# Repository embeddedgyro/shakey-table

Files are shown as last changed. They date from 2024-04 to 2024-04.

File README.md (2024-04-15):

# Introduction
Welcome to the shakey-table GitHub page, developed by Adam Englebright, Torin Storkey, Gennady Magin, and Jambulingam Kothandapani.

As part of the Real Time Embedded Programming 5 course at the University of Glasgow,
we have been tasked with developing a project that requires real time programming under GNU/Linux on a Raspberry Pi.
The project we have decided on is a self-balancing cup holder, implemented using a reaction wheel.
Essentially, an inverted pendulum. This git repository contains the code required to run this
self-balancing cup holder and instructions on how to build it for both software and hardware.

We used a Pi 5, which introduced some extra challenges as its GPIO differs greatly from
previous versions, meaning that common libraries like `pigpio` would not work.
This project was only tested on a Pi 5 using the latest Raspberry Pi OS
(`uname -a` output: *Linux rpi5-2 6.6.21-v8-16k+ #1 SMP PREEMPT Tue Mar 12 11:01:10 UTC 2024 aarch64 GNU/Linux*).
We cannot guarantee that it will work on other versions of the Pi or on other operating systems
or OS versions.

# Software
## Prerequisites/Dependencies
The following Debian packages (Raspberry Pi OS is built on Debian and has access to Debian packages) are required for this program to build and run on a rpi5:
* `linux-libc-dev`
* `libi2c-dev`
* `make`
* `cmake`
* `g++`

The following packages are recommended:
* `git` for cloning the repository, although you can simply download the code from the GitHub website if you wish.
* `doxygen` for creating nice documentation from the comments in the code.
* `texlive-full` for compiling a PDF document from the LaTeX code created by Doxygen (which also creates a website that you can view in your browser,
so this is not necessary to view the documentation).

These packages can be installed using `sudo apt install <package name>`.

There are also installs required that cannot be found in the standard repos, primarily due to the use of a Pi 5:
* `libgpiod` v2 is required. However, the version on the Debian Bookworm repo as of 2024-03-03 is v1.6.3 (despite the package name being `libgpiod2`).
This must be installed from source. `git clone git://git.kernel.org/pub/scm/libs/libgpiod/libgpiod.git`
([repo link](https://git.kernel.org/pub/scm/libs/libgpiod/libgpiod.git/)) in a suitable place and follow the `README` instructions.
The advised options to pass to the `autogen.sh` script are `--enable-tools=yes` (not *necessary*, but provides useful command line tools)
and `--enable-bindings-cxx` (**necessary**, since this is a C++ program). Note that to build with C++ bindings, the `autoconf-archive` package is required
(this can be easily `apt install`'d from the Debian repos). You may also need to `apt install` the `libtool` package for the build to work.
* As of the latest kernel for the Pi 5 on 2024-04-03 (6.6.21-v8-16k+), this patch is required for PWM to work through the sysfs interface:
[https://github.com/raspberrypi/linux/pull/6026](https://github.com/raspberrypi/linux/pull/6026). Install using `sudo rpi-update pulls/6026`.
See [https://forums.raspberrypi.com/viewtopic.php?t=359251](https://forums.raspberrypi.com/viewtopic.php?t=359251),
particularly the [post by neuralassembly](https://forums.raspberrypi.com/viewtopic.php?p=2202349#p2202349) and onward.

### config.txt
To enable the I2C and PWM hardware on the Raspberry Pi 5, the following lines must be added to your `/boot/firmware/config.txt`:
* `dtparam=i2c_arm=on`
* `dtparam=i2c_vc=on,i2c_vc_baudrate=400000`
* `dtoverlay=pwm-2chan`

Remember to reboot your Pi after entering these lines. The `config.txt` used on our Pi can be found in the root of this repo.

## Building the Software
To build the software, follow these instructions:
* `git clone https://github.com/embeddedgyro/shakey-table.git`
* `cd shakey-table`
* `mkdir build` (It is advisable to create an *out-of-source* build, hence this and the following step.)
* `cd build`
* `cmake ..`
* `make`

After this, an executable program called **ShakeyTable** should exist under the `build/src/` directory.
That is, `build/src/ShakeyTable`. This program can be run by entering either the absolute or relative
path of the executable. For example, `/some/path/from/root/shakey-table/build/src/ShakeyTable`, or
`src/ShakeyTable` if you are still in the `build` directory. If you are in the same directory as the
executable, you can enter `./ShakeyTable` (the leading dot means *this directory*).

In addition to the main **ShakeyTable** executable, there will also be a **ShakeyTable_no_INA**
executable. This runs a version of the main program that doesn't use the INA260 current sensor
for torque control. Instead, it only uses the MPU6050 and a single PID controller for position control.
This program was developed as a backup in case the INA260 could not be configured to
work with the motor driver operating in both directions
([see the wiki](https://github.com/embeddedgyro/shakey-table/wiki/Hardware-Woes#the-ina260-current-sensor)).

There will also be two executables for testing the functionality of the MPU6050 and INA260,
named **mpu_testing** and **ina_testing**, respectively. **mpu_testing** will communicate with
the MPU6050 and continuously write the measured angular position to the screen.
**ina_testing** will do the same with the INA260, continuously writing out the measured
current to the screen. These test programs are useful for confirming that the sensors
have been correctly connected to the Pi and are functioning properly.

## Documentation
Documentation of this project is provided by Doxygen formatted comments in the code.
Doxygen can be used to create a website and PDF document that organise the documentation
in a way that is clear, easy to navigate, and easy to read.

### Master Release Documentation
To see the the documentation for the latest release of shakey table the documentation can be found [here](https://shakeytable.guengineering.co.uk/).

### Self Hosted Website
To create the documentation website for personal forks and development builds, run `make doc` after the `cmake ..` command from the above build instructions.
Running `cmake ..` will create a Doxyfile, and running `make doc` will run Doxygen on this file to generate
the documentation website under the `build/html/` directory.

To view this website, open your browser of choice.
In the URL bar, enter `file:///some/path/from/root/shakey-table/build/html/index.html`. This will open the
main page of the website. From there you can find the rest of the documentation using the navigation
tools at the top of the page.

### PDF Document
After running `make doc`, there will also be a `build/latex/` directory. If you have a TeX distribution
installed, you can `cd` into this directory and enter `make`. This will invoke `pdflatex` to generate
a PDF document called `refman.pdf`, which will contain the Doxygen generated documentation for the project.
View with your PDF reader of choice. Most browsers can also view PDF documents.

# Unit Testing
ShakeyTable on the whole has three modules namely `MPU6050`, `INA260` and `Cytron MD20A` along with PID control functionality. When developing unit testing we intend to validate each module's functionalities by a specific set of test cases and consolidated them into `Online` and `Offline` testing based on its nature of examination. Online unit testing validates  each module's communication status to raspberry pi through i2c bus. Hence to run online testing each module has to be configured into the overall setup and actively involved in communication. On the other hand offline testing intend to validate the static functionalities of the software, examining the expected output against the module's program output. These testing can be validated when the setup is offline to ensure proper functioning of the software.
	
## Building Unit Tests
Follow the software building procedure as mentioned before which includes cloning the repo and building the system through commands `cmake .. make`. This will generate the executable files for each module's unit testing functions. Now type `ctest` in the same directory to view the results of both online and offline testing together. You can also view the results of either one testing through the command `ctest -R online` or `ctest -R offline` which executes only the files associated to those testing. Individual executable files for concern modules can be found in the directory `./test/****/**`. Here `./` indicates that you are required to be currently in `build` directory and `****` indicates the module that you intended to view the executables (eg., mpu6050, ina260) and `**` specifies the specific test file executable.
	eg., `./test/mpu6050/mpu6050_AccelOffset_ut`.

## Unit Testing Output
Each unit test will either pop `Passed` if successfully executed without exception or `Subprocess aborted***Exception:` with the exception scenario encountered if failed.

# Hardware

## Components

This section describes hardware components used in this project, and what is their purpose. Descritions are followed by links to datasheets for those components and information about how they should be wired and positioned on a physical prototype. All supporting reference images for this section can be found in "Hardware Assembly" section of this README.

The following components were used for this project:

* Microcontroller - Raspberry Pi 5. Used for executing the main program and interfacing with sensors and motor driver.

Documentation for it can be found here [https://www.raspberrypi.com/documentation/](https://www.raspberrypi.com/documentation/).

* Current Sensor - INA260. Used for reading current flowing through the motor for PID motor control as current is proportional to the torque generated by the motor. Uses I2C communication protocol for interfacing with Pi.

Datasheet can be found here [https://www.ti.com/lit/ds/symlink/ina260.pdf](https://www.ti.com/lit/ds/symlink/ina260.pdf).

Should be connected in series with the motor. Vin- terminal is connected to the white wire on the motor and Vin+ is connected to the MB terminal of the motor driver. Powered by a 3V3 supply from the Pi. Communicates with the Pi through I2C1 pins (SDA->gpio0, SCL->gpio1) which don't have internal pull-up resistors, but there are pull-up resistors inside the current sensor, so that should not be a problem. The Alert pin is connected to gpio5 on the Pi.

* Gyro-Acelerometer Sensor - MPU6050. Measures the acceleration of the table in a 2D plane and subtracts the centripetal acceleration from it to get the acceleration due to gravity. Measurements are used for PID motor control. Uses I2C communication protocol for interfacing with Pi.

Datasheet can be found here [https://mm.digikey.com/Volume0/opasdata/d220001/medias/docus/2204/SEN0142_Web.pdf](https://mm.digikey.com/Volume0/opasdata/d220001/medias/docus/2204/SEN0142_Web.pdf).

Should be mounted firmly to the surface of the table with connection pins facing the ground. Position reference image can be found in "Hardware Assembly" section of the README. Powered by a 3V3 supply from the Pi. Communicates with the Pi through I2C0 pins (SDA->gpio2, SCL->gpio3) which have internal pull-up resistors. No extra external circuitry is needed. Interrup pin should be connected to gpio4.

* Motor Driver - Cytron MD20A. Regulates voltage supplied to the motor. Controls the direction and speed of motor rotation with PWM.

Datasheet can be found here [https://robu.in/wp-content/uploads/2019/05/MD20A-Datasheet.pdf](https://robu.in/wp-content/uploads/2019/05/MD20A-Datasheet.pdf).

Uses a 12V external DC power supply connected to VA+ and VB- for delivering power to the motor. In this project, an external power generator was used for this purpose. Use thick multicore wires with good isolation for power lines. Controls the motor rotation by receiving a 20kHz PWM signal with a PID-controlled Duty Cycle from gpio18 on the Pi. Direction is controlled by a High-Low output from gpio23 into the DIR pin on the motor driver.

* Motor - 12V DC Motor 12kg-cm 350RPM w/Encoder. Used for rotating the reaction wheel and creating the necessary torque for table stabilisation.

 Device specifications are mentioned on this website [https://uk.robotshop.com/products/12v-dc-motor-12kg-cm-350rpm-encoder](https://uk.robotshop.com/products/12v-dc-motor-12kg-cm-350rpm-encoder).

The  white motor wire should be connected to the Vin- terminal on the INA260, and red motor wire should be connected to the junction between the capacitros and inductors inside the LC filter.

* Low-Pass Filter (optional element) - LC filter with a cut-off at about 1200Hz to eliminate high-frequency noise coming from the motor driver and Pi PWM signal.

Uses two 560uH choke inductors(`MCAP115018077A-561LU`) after MA terminal on the motor driver in series with the motor (connect to red motor wire) and the current sensor. Seven 2.2uF polyester film capacitors(`7212-707`) are connected after inductors in parallel around the current sensor and motor driver. At high frequencies, the inductor becomes very resistive and blocks high-frequency signals from passing into the circuit. The capacitor becomes a short circuit for high-frequency signals. High frequencies flow through it, avoiding the current sensor and the motor. Inductors with a high current rating above 10A and capacitors with a high voltage rating above 20V should be used in this project to prevent damage and burning of the filter. Polarised capacitors cannot be used, as current can flow in both directions in this circuit.

WARNING! If there is not a lot of noise that disrupts current sensor readings, we reccommend not to use this compoenent as it might cause I2C communication issues and damage sensors due to high current and voltage spikes during the switching of the direction and duty cycle of motor rotation.

## Hardware Assembly

This section contains all reference image materials for wiring and positioning hardware components.

This image represents the wiring of the whole setup:
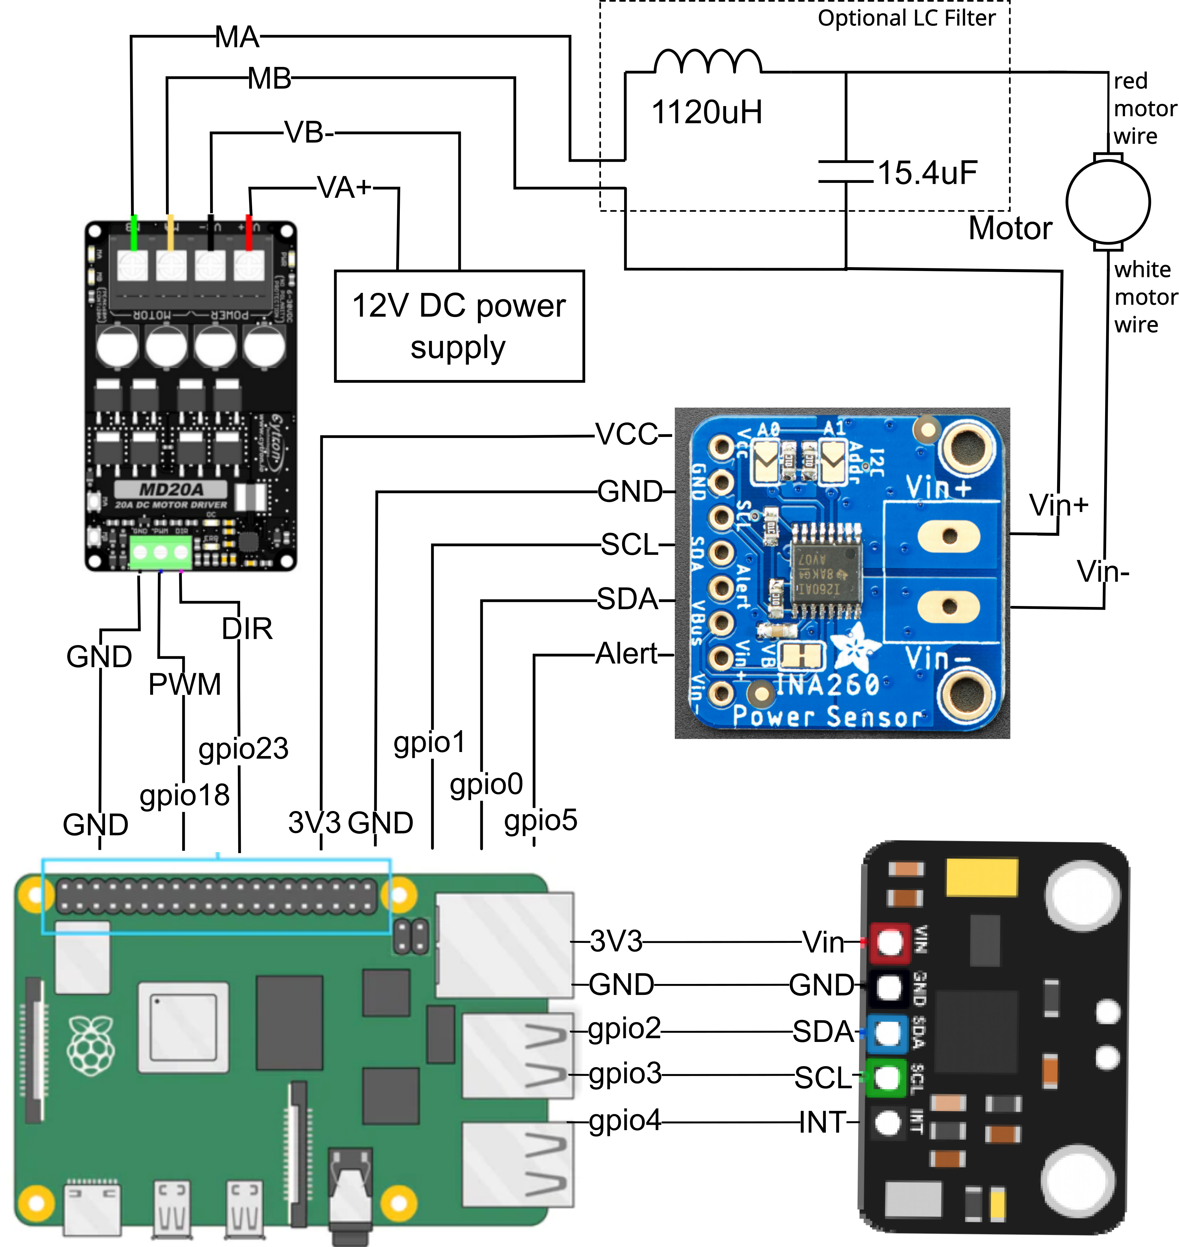
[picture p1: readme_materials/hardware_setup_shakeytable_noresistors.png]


This image shows pin configuration on the Raspberry Pi 5 for assembly:
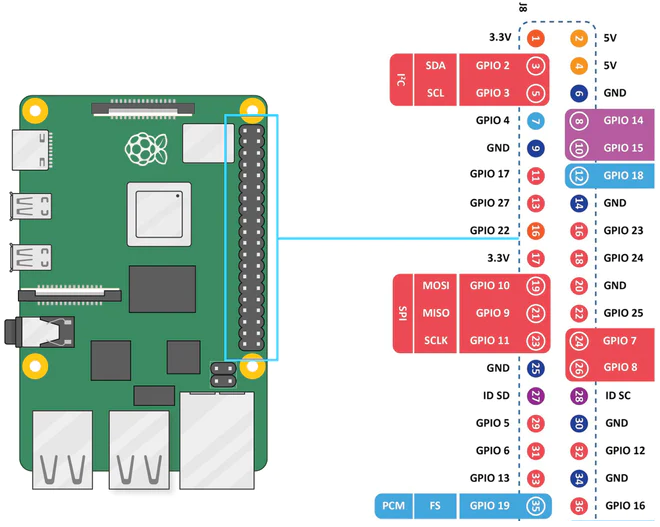
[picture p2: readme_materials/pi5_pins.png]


This image shows the correct position of the gyro-accelerometer on the shakey table:
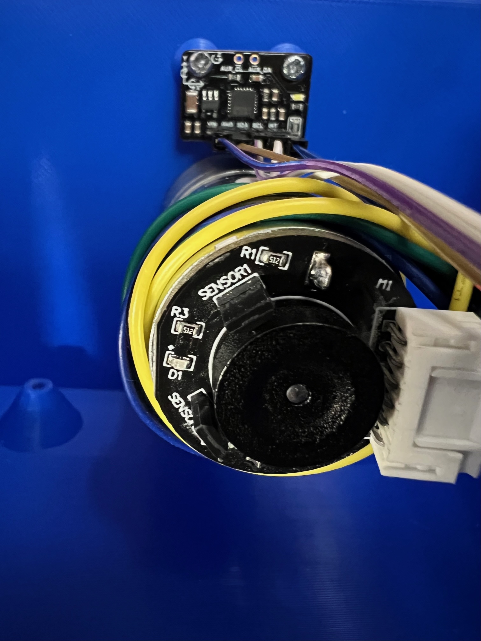
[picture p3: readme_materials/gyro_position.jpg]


## CAD Design

For the cad design a [OpenSCAD](https://openscad.org/) was used. OpenSCAD is an open source parametric CAD program. It has a programming language that it uses for defining the 3d design of objects. It is good for customisable designs. In the cad directory you can see the design file for the shakey table including the wheel lid and frame. The design includes mounting points for the mpu6050, the motor and the raspberry pi. Then a lid for the cup to rest on. Also the wheel has holes to allow bolts to be inserted to vary its moment of inertia. 

# Social Media 

Our project was advertised via Instagram [https://www.instagram.com/antiquakegu/](https://www.instagram.com/antiquakegu/) and Twitter [https://twitter.com/shakey_table](https://twitter.com/shakey_table).

Instagram was our main target. We got 120 followers, out of which 50 were constantly active, reacting on our stories, supporting us in the comments and liking our posts. Our strategy was to start advertysing our project when we were ready to start building and testing our prototype with actual hardware, as general audience is not interested in the coding side of the project on social media. We started advertising our product when we had our project fully planned and ready on the software side. 

We were posting stories of our work on the prototype every 2-3 days (you can see some of them in the highlights section called "project dev"), and tried to guide our audience through different development stages of the protype, share our wins, failiures and soltions to problems we faced on our path. We were also releasing 2 posts a week that summerised our main achievements and familiarised people with what we were actually doing. We tried to make it as non-technical as possible not to bore people with unnessessary details, but we were always happy to answer any questions in the comments.

The Instagram "Reel" with prelimenary functionality of our table recieved more than 15k views in the first 24 hours after release.

Our Instagram page:
plot

Reels on Instagram:
plot

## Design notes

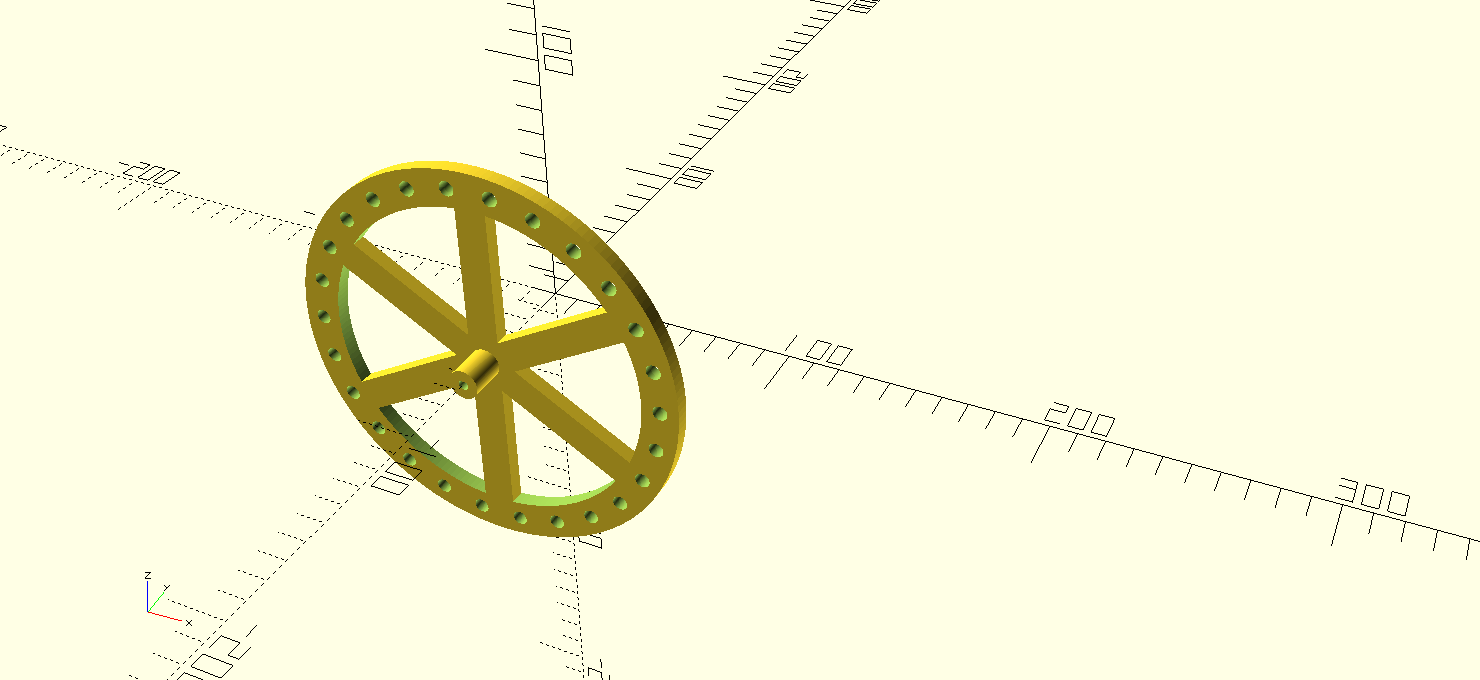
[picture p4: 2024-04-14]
cad/design.png

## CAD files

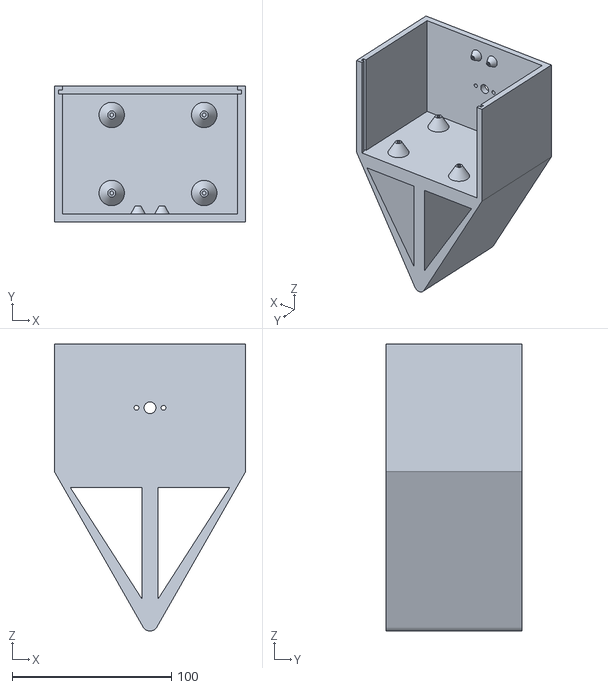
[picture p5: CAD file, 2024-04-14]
cad/frame.stl
120.0 x 85.0 x 180.0

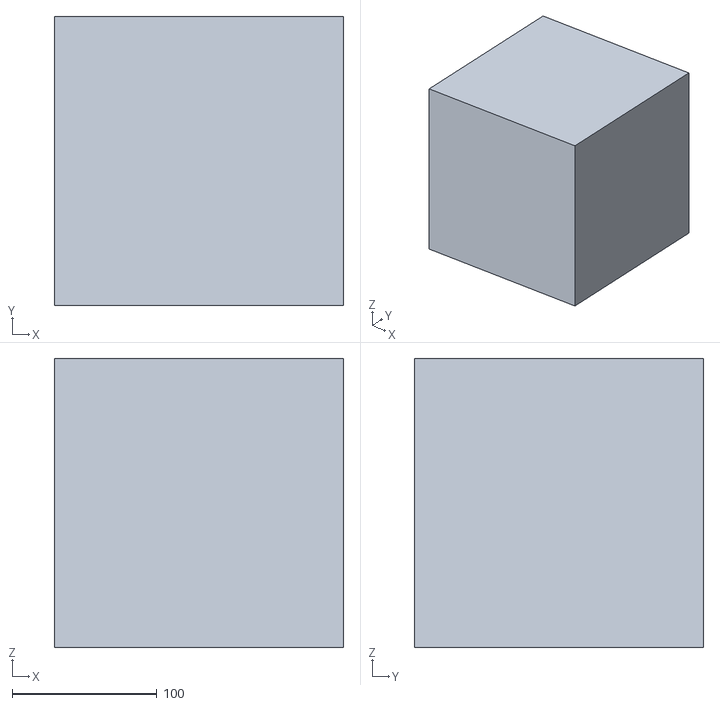
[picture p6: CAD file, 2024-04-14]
cad/cube.stl
200.0 x 200.0 x 200.0

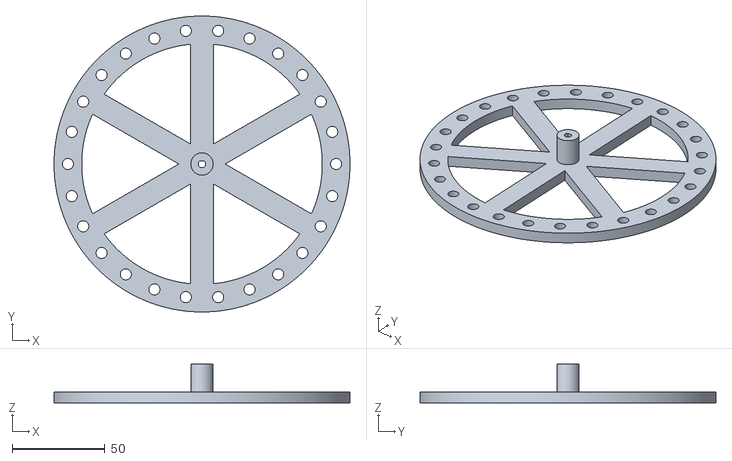
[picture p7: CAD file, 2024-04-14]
cad/wheel.stl
160.0 x 160.0 x 21.0

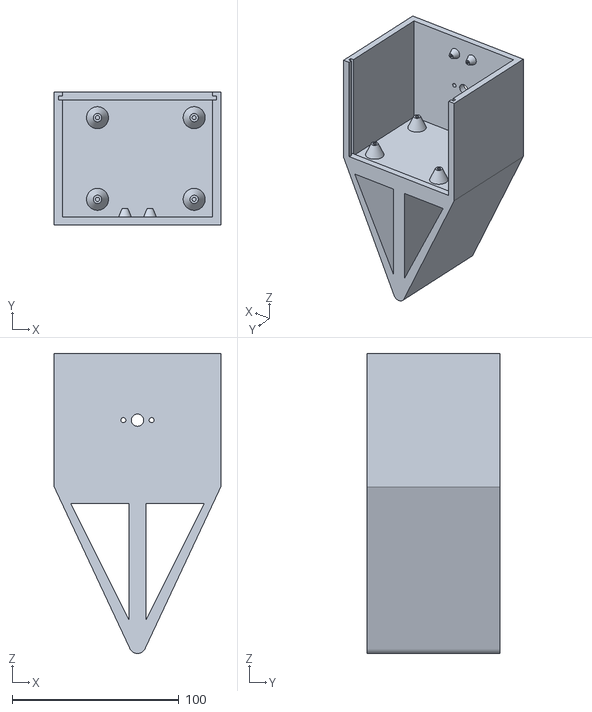
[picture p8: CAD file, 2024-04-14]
cad/design.stl
100.0 x 80.0 x 180.0

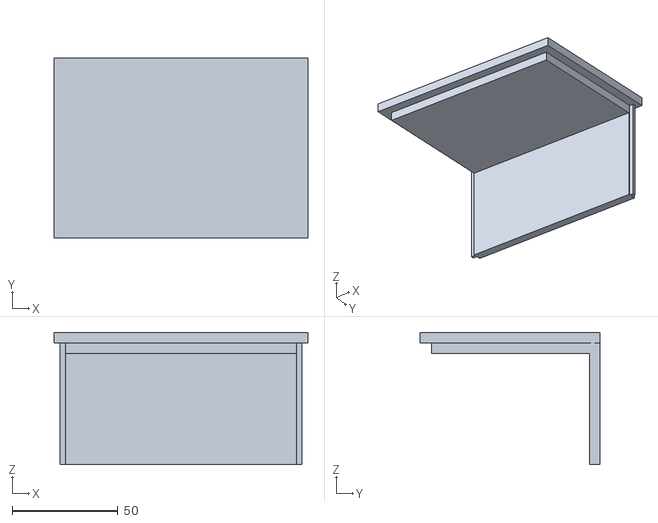
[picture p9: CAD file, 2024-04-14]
cad/lid.stl
120.0 x 85.0 x 62.5

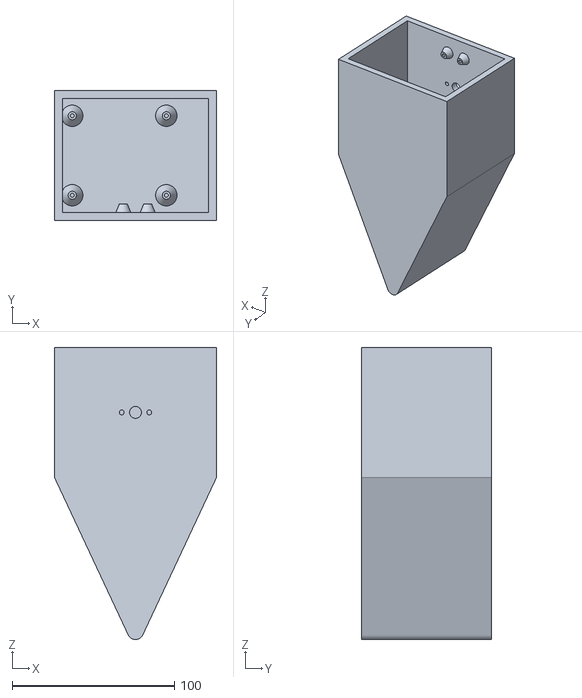
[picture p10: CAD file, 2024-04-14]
cad/housing.stl
100.0 x 80.0 x 180.0

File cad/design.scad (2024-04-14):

$fs=0.25;
$fa=2;
width = 120;
depth = 85;
height = 80;
slot_thick = 30;
bottom_rad = 5;
tri_height = 100;
wheel_rad = 80;
wheel_thick = 6;
wheel_rim_width = 15;
n_spokes = 6;
n_bolts = 26;
slot_height = 22.5;
bolt_rad = 6/2;
mpu_bol_rad = 3.5/2;
mpu_width = 15;
wall_width = 5;
mot_scale = 1.05;
amot_len=52;
amot_d=25;
spoke_thick = 12.5;
shaft_rad = 4/2;
shaft_cut = 2*shaft_rad-3.5;
mot_len = mot_scale*amot_len;
mot_d = mot_scale*amot_d;
mot_r=mot_d/2;
amot_nib_d = 7;
amot_nib_len=12;
offset_dist = 10;
mot_nib_len = mot_scale*amot_nib_len;
mot_nib_d = mot_scale*amot_nib_d;
mot_nib_r=mot_nib_d/2;
tri_hyp = sqrt(tri_height^2+(width/2)^2);
mot_bol_of=17/2;
mot_bol_r=1.5;
pi_pos=[[0,0],[0,49],[58,0],[58,49]];
module pi_standoff(d=2.5,sheight=10){
    translate([0,0,-1])
    difference(){
    cylinder(h=1+sheight,r2=d,r1=d+(2*sheight/3));
    translate([0,0,2])cylinder(h=1+sheight,r=d/2);
    }
    }
module tricut(){
    polygon([[offset_dist/2,offset_dist],[width/2-offset_dist,offset_dist],[offset_dist/2,tri_height-2*offset_dist]]);
    }
//base
module base(){
difference(){
union(){
difference(){
difference(){
union(){
cube([width,depth,height],center=true);
translate([0,-depth/2,-height/2])rotate([-90,0,0])
    linear_extrude(depth)
    difference(){
    hull(){
        polygon([[width/2,0],[-width/2,0],[0,tri_height/2]]);
        translate([0,tri_height-bottom_rad])circle(r=bottom_rad);}
        union(){
            tricut();
        mirror([1,0,0]){
            tricut();
        }
     }
    }
}
translate([0,0,2])cube([width-2*wall_width,depth-2*wall_width,height+2],center=true);
}
translate([0,wall_width-depth/2+mot_len,0])rotate([90,0,0])
union(){
cylinder(h=mot_len,r=mot_r);
translate([0,0,mot_len-1])
    union(){
        cylinder(h=mot_nib_len+1,r=mot_nib_r);
        translate([mot_bol_of,0,0])cylinder(h=mot_nib_len+1,r=mot_bol_r);
        translate([-mot_bol_of,0,0])cylinder(h=mot_nib_len+1,r=mot_bol_r);
    }
}
}
translate([-5,0,0])
rotate([0,0,180])
translate([3.5-85/2,3.5-56/2,-height/2])
for(pos=pi_pos){
   translate([pos.x,pos.y,0])pi_standoff();
}
translate([0,-depth/2+wall_width,height/3])rotate([-90,0,0])
union(){
    translate([mpu_width/2,0,0])pi_standoff(sheight=5, d= mpu_bol_rad);
    translate([-mpu_width/2,0,0])
    pi_standoff(sheight=5, d=mpu_bol_rad);
}

}
translate([0,0,wall_width/2])
union(){

union(){
translate([0,0,height/2])cube([width-2*wall_width,depth-2*wall_width,wall_width*2], center=true);
translate([0,0,(height+wall_width)/2])cube([width,depth,wall_width], center=true);
};
translate([0,(depth-wall_width)/2,-wall_width/4])
union(){
translate([0,-wall_width/4,0])cube([width-wall_width,wall_width/2,height],center=true);
cube([width-2*wall_width,wall_width,height],center=true);
}}}
}
//wheel
module react_wheel(){
difference(){
difference(){
union(){
difference(){
    cylinder(h=wheel_thick, r = wheel_rad,center=true);
    cylinder(h=wheel_thick+2, r= wheel_rad - wheel_rim_width,center=true);
    
}
for (i=[0:n_spokes/2]){
    rotate([0,0,i*(360/n_spokes)])cube([spoke_thick,2*(wheel_rad-wheel_rim_width),wheel_thick],center=true);
}
}
for(i=[0:n_bolts]){
    rotate([0,0,i*(360/n_bolts)])translate([wheel_rad-wheel_rim_width/2,0,0])cylinder(center=true,h=wheel_thick+2,r=bolt_rad);
}
}
difference(){
cylinder(h=wheel_thick+2,r=shaft_rad,center=true);
translate([0,3*shaft_rad/2-shaft_cut,0])cube([2*shaft_rad,shaft_rad,wheel_thick+4],center=true);
};
}
}
module wheel(){
translate([0,-3-depth/2-wheel_thick/2,0])rotate([90,0,0])
union(){
scale([1,1,3])
translate([0,0,wheel_thick/2])
intersection(){
    react_wheel();
    cylinder(r=shaft_rad*3,h=40,center=true);
}
react_wheel();
}
}

//lid
module lid(){
union(){
translate([0,0,0]){
union(){
translate([0,0.2,height/2])cube([width-wall_width*2-0.8,depth-wall_width*2-0.4,wall_width*2], center=true);
translate([0,0,(height+wall_width)/2])cube([width,depth,wall_width], center=true);
};
translate([0,(depth-wall_width)/2,slot_height/2])
union(){
translate([0,-wall_width/4+0.4,0])cube([width-wall_width-0.8,wall_width/2-0.8,height-slot_height],center=true);
    cube([width-2*wall_width-0.8,wall_width,height-slot_height],center=true);
}}}
}
lid();
base();
wheel();

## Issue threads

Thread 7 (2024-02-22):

Implement control for MPU6050 (IMU)

Adam-Englebright, 2024-02-22:
### Why?
Our program must be able to interface with the MPU6050 6-axis IMU to access acceleration and angular velocity data, to identify the position of the cup holder. This position will then be fed into a PID controller to control the motor driving the reaction wheel.

### How?
There are libraries available for interfacing with the MPU6050 from a Raspberry Pi, but a quick inspection indicates that they may not have the full functionality required, particularly for using an interrupt driven approach (more research required). Regardless, they will serve as a good basis for our own implementation, which could be a slightly modified version of one of the libraries. The libraries investigated so far:
- [MPU6050-Sensor-Library-Cpp](https://github.com/batu92k/MPU6050-Sensor-Library-Cpp/blob/master/LICENSE)
- [MPU6050-C-CPP-Library-for-Raspberry-Pi](https://github.com/alex-mous/MPU6050-C-CPP-Library-for-Raspberry-Pi)

Closed 2024-02-29.

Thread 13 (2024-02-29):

Implement control for MD20A (motor driver)

genamag, 2024-02-29:

Jambu1234, 2024-03-13:
https://github.com/embeddedgyro/shakey-table/pull/18
Pull request for Motor driver control implementation code.

genamag, 2024-03-29:
The code is fully written, has all the comments and is styled properly.

The next step is testing it during the implementation stage

Closed 2024-03-29.

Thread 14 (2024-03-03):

CMake and Unit testing

Jambu1234, 2024-03-03:
Working on incorporating CMake build system to our overall project module and developing unit tests for each modules.

Jambu1234, 2024-03-29:
Unit test case developed for PID controller with customized input values.

Jambu1234, 2024-04-11:
Unit tests has been classified as online and offline testing validating modules communication attributes through i2c bus via online testing and methods intended static functioning through offline testing. Modules like MPU6050 and INA260 has been online tested, followed by MotorDriver and PID control is validated through offline testing.
CMake file structure is updated to validate the unit testing in a single go.

Jambu1234, 2024-04-11:
Unit testing task has been successfully completed as defined.

Closed 2024-04-11.

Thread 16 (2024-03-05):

unit test for PID controller

genamag, 2024-03-05:
write a unit test with known values of inputs into the controllers, set gains and dt. Make sure that calculated outputs match the theoretical predictions.

Jambu1234, 2024-04-08:
PID Unit testing is created and validated

Closed 2024-04-08.

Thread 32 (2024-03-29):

change README for MotorDriver code

genamag, 2024-03-29:

genamag, 2024-04-13:
this is a useless issue, as we will have all hardware and software details in the main README, so there is no need of creating a separate one

Closed 2024-04-13.

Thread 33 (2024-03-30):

There needs to be a main program.

Adam-Englebright, 2024-03-30:
We need an actual program that utilises our libraries to interface with the MPU6050, INA260, and MD20, to drive our anti-quake cup holder. That is, read accel and gyro data from the MPU6050, calculate the cup holder angle/position, then drive the MD20 to produce the required corrective torque from the motor, using the INA260 data as torque feedback data.

genamag, 2024-04-13:
the main program is done and tested, everything works as intended after we  replaced faulty components

there is only a problem of occasional I2C errors, in sensor communication, but they do not disrupt the functioning of the main program and don't affect performance, as sensor readings are sent with very high freqeuncy

genamag, 2024-04-13:
Because we fried the INA260 current sensor, we can only control the wheel with PID control from gyro readings, so there is no good control over the torque produced by the motor

Closed 2024-04-14.

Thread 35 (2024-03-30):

Bring everything together and control a self-balancing cup holder

Adam-Englebright, 2024-03-30:

genamag, 2024-04-08:
Fully assembled the device with CAD elements and all the circuitry

Tested the functionality of sensors, motor driver and PID control

genamag, 2024-04-08:
now on the stage of testing, tuning and debugging main program

genamag, 2024-04-13:
the main program works, we just need to tweak PID control parameters

but we fried out MPU, so we might need to control our motor only with outputs from MPU6050

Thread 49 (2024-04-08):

Create a proper README file with hardware and software instruction

genamag, 2024-04-08:
Torin - CAD design
Gennady - Hardware setup
Adam - Software setup and installation
Jambu - Running Unit testing

genamag, 2024-04-13:
Added a hardware description with all components and what they are doing + how to connect. Also created and added images of the circuitry and positioning of key components

genamag, 2024-04-13:
yesterday we changed the position of the INA from before to after the motor to protect it from the reverse bias current created by the filter, so I need to reflect that in Wiki, change images and README in terms of this modification to the circuitry

genamag, 2024-04-13:
@dalvador2 How is the CAD and INA software part doing?
@Jambu1234 How is Unit testing part doing? (don't forget about writing about CMake for them as well with instructions on how to run them?
@Adam-Englebright how is the MPU6050 and main program section doing?

Please, report on your progress

Adam-Englebright, 2024-04-13:
The section on setting up the software is essentially done. I want to add details about the lines required in `/boot/firmware/config.txt`.

Jambu1234, 2024-04-13:
Readme for Unit testing execution has been updated with the necessary cmake comments to run them.

dalvador2, 2024-04-14:
closed #61

Closed 2024-04-14.

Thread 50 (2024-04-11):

Noisy PWM output from Raspberry Pi

Jambu1234, 2024-04-11:
PWM output from Raspberry Pi which is required to be controlling the motor driver has noise associated with it.

genamag, 2024-04-13:
turned out that the Raspberry Pi 5 was broken. Changing the pi to a new one fixed the issue with wrong duty cycle and shape of  PWM signals on the output

Closed 2024-04-13.

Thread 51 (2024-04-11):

Detached Reaction Wheel from Motor

Jambu1234, 2024-04-11:
Reaction wheel which is intended to be changing its rotational direction based on the cup holder's position got detached and deformed.

Jambu1234, 2024-04-11:
Expected scenario : 3D printed Reaction wheel has been screwed with M6 bolts of around 20 sets to make it weigh more. It was expected that heavy reaction wheel could assist us in imparting counter rotation enabling the cup holder returning back to its neutral position.

Concern : Heavy wheel mounted onto the motor driver couldn't with stand the instantaneous change in motor driver rotational direction due to its inertia, causing it tear down from the setup.

Jambu1234, 2024-04-11:
Solution: We addressed the issue by reprinting the reaction wheel with lighter weight, achieved by reducing the 3D printing fill density. Additionally, we minimized the number of bolts attached to the wheel.

Closed 2024-04-11.

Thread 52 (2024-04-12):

The INA260 stops working when the motor driver is driven in one of two directions

Adam-Englebright, 2024-04-12:
The INA260 will work just fine when the motor driver is driven in one direction, but will break down once the direction is switched. I2C communication will stop working and current readings will be nonsense.

Adam-Englebright, 2024-04-12:
The problem has been discovered and documented in the [wiki](https://github.com/embeddedgyro/shakey-table/wiki/Hardware-Woes#the-problem). In short, our circuit has damaged our INA260 to a non-functional state. We now need to try balancing control using just the MPU6050 and the angular position it measures.

Closed 2024-04-12.

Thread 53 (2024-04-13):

First number calculated for the angular position is `nan`, causing a duty cycle out-of-bounds exception in the motor driver code

Adam-Englebright, 2024-04-13:
As in the title. The first time running any program that reads from the MPU6050 and calculates the angular position will fail with an exception from the motor driver control code (desired duty cycle out-of-bounds). **All subsequent program runs work fine, with no exception thrown**.

Closed 2024-04-13.

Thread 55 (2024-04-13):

prototype is unbalanced

genamag, 2024-04-13:
the table is tipping over on the wheel side because the centre of mass is high up and is moved towards the front side. We need to add some weight on the low rear side to balance it out and make it more stable

genamag, 2024-04-13:
Added heavy choke inductors to the bottom of the inner walls of the table's base. Attached them with tape. It holds fine and the table is not tipping over anymore

Closed 2024-04-13.

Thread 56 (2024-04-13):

the wheel is still falling off during thesting because of high torque

genamag, 2024-04-13:
need to find a way to fix the wheel on the motor shaft so that it holds in place during testing

genamag, 2024-04-13:
attached the wheel with super glue, it seems to hold just fine. We also minimised max duty cycle to 0.5 to minimise the maximum torque created not to break the last remaining 3D-printed wheel

genamag, 2024-04-13:
Even if the glue holds the wheel in place, there is still some torque and friction happening, which just melts down the glue, and it stops doing its job.

Solution: don't test it for too long and make breaks between tests to make sure that the glue hardens again

Closed 2024-04-13.

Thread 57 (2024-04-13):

wires are too short

genamag, 2024-04-13:
need to elongate them, or otherwise, they are strained during testing when the table moves around

genamag, 2024-04-13:
elongated the wires with crocodile clips and pairs of mother-mother father-father connectors

Closed 2024-04-13.

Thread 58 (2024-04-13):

Issue with I2C communication with MPU6050

genamag, 2024-04-13:
When we test the prototype, at the equilibrium point the wheel started vibrating like crazy due to PID control, and then we started seeing errors in I2C communication between the Pi and the sensor.

Restarting the MPU fixes it, but the issue comes back during every test run

We don't know if it is a hardware or a software issue for now

genamag, 2024-04-13:
the issue was the LC filter, not physical vibrations. Fast ripples in the current through the motor probably caused a lot of voltage and current spikes in the passive components, which in turn disrupted the fragile I2C communication

getting rid of the LC filter in the circuit completely eliminated the issue

Closed 2024-04-13.

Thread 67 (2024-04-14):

PID unit test - Failing

Jambu1234, 2024-04-14:
PID unit test which does the offline testing of PID source code fails.

Jambu1234, 2024-04-14:
Concern : Offline PID unit test comparing the computed and expected value fails though the printed output value seems the same.

Cause : PID output involves computation of multiple floating point variables. Manual calculation of expected value involved floating point round-off which caused the mismatch between the expected and the actually computed value.

Solution : Updated the expected value to its hexadecimal representation so that floating point round-off concern can be resolved.

Closed 2024-04-14.

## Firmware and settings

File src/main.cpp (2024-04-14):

/**
 * @file    main.cpp
 * @author  Adam J. Englebright
 * @date    30.03.2024
 * @brief   This file constains the main program that controls the anti-quake cup holder.
 *
 * Copyright 2024 Adam J. Englebright <adamenglebright@rocketmail.com>
 *
 */

#include <cmath>
#include <fstream>
#include <limits>
#include <thread>
#include <chrono>
#include <iostream>
#include "../lib/pid/pid.h"
#include "../lib/mpu6050/mpu6050.h"
#include "../lib/i2c_interface/smbus_i2c_if.h"
#include "../lib/ina260/ina260.h"
#include "../lib/MotorDriver/MotorDriver.h"


/**
 * @brief Implementation of the PID_Interface for the inner PID controller,
 * driving the motor driver.
 */
class PID_MotorDriver : public PID_Interface
{
public:
  /**
   * @brief Constructor taking and assigning a motor driver object reference.
   * @param _motorDriver The motor driver object.
   */
  PID_MotorDriver(MotorDriver& _motorDriver) : motorDriver(_motorDriver) {}
  
  /**
   * @brief PID controller callback implementation, passing the PID output to the provided motor driver object.
   * @param pidOutput Output of the PID controller passed to the callback.
   */
  virtual void hasOutput(double pidOutput) override {
    motorDriver.setDutyCycleDelta(-pidOutput); // If corrective torque is positive, then we need to change duty cycle by a negative amount, and vice versa.
    log_file << pidOutput << std::endl;
  }

private:
  /**
   * @brief Output file stream for logging inner PID outputs.
   */
  std::ofstream log_file{"Inner_PID_log", std::ios::trunc};
  
  /**
   * @brief Motor driver object reference attribute.
   */
  MotorDriver& motorDriver;
};


/**
 * @brief Implementation of the PID_Interface for the outer PID controller,
 * controlling position via torque outputs that are sent to the inner PID
 * controller.
 */
class PID_Position : public PID_Interface
{
public:
  /**
   * @brief Constructor taking and assigning a PID controller object reference.
   * @param _pidController The PID controller object.
   */
  PID_Position(PID& _pidController) : pidController(_pidController) {}
  
  /**
   * @brief PID controller callback implementation, passing the PID output to the provided PID controller object.
   * @param pidOutput Output of the PID controller passed to the callback.
   */
  virtual void hasOutput(double pidOutput) override {
    pidController.setSetpoint(pidOutput);
    log_file << pidOutput << std::endl;
  }

private:
  /**
   * @brief Output file stream for logging outer PID outputs.
   */
  std::ofstream log_file{"Outer_PID_log", std::ios::trunc};
  
  /**
   * @brief PID controller object reference attribute.
   */
  PID& pidController;
};


/**
 * @brief Implementation of the INA260Interface for feedback of current (torque)
 * values as the process variable for the inner PID controller driving the motor driver.
 */
class INA260_Feedback : public INA260_Driver::INA260Interface
{
public:
  /**
   * @brief Constructor taking and assigning a PID controller object reference.
   * @param _pidController The PID controller object.
   */
  INA260_Feedback(PID& _pidController) : pidController(_pidController) {}

  /**
   * @brief INA260 callback implementation, passing the measured current (torque) to the provided PID controller object.
   * @param sample Current measured by the INA260 passed to the callback.
   */
  virtual void hasSample(INA260_Driver::INA260Sample& sample) override {
    pidController.calculate(sample.current);
    //std::cout << "INA callback called. Data: " << sample.current << std::endl;
    log_file << sample.current << std::endl;
  } // May want a scale factor to convert current -> torque (or just adjust PID constants)

private:
  /**
   * @brief Output file stream for logging INA measurements.
   */
  std::ofstream log_file{"INA_log", std::ios::trunc};
  
  /**
   * @brief PID controller object reference attribute.
   */
  PID& pidController;
};


/**
 * @brief Implementation of the MPU6050Interface. This is where the magic
 * happens for calculating the cup holder's angular position based on the IMU
 * measurements. The caclulated angular position is then sent as input to the
 * outer PID controller as the process variable.
 */
class MPU6050_Feedback : public MPU6050_Driver::MPU6050Interface
{
public:
  /**
   * @brief Constructor taking and assigning a PID controller object reference.
   * @param _pidController The PID controller object.
   * @param _radius Distance between MPU and axis of rotation.
   * @param _samplePeriod Time between samples.
   */
  MPU6050_Feedback(PID& _pidController, float _radius, float _samplePeriod)
    : pidController(_pidController), radius(_radius), samplePeriod(_samplePeriod) {}

  /**
   * @brief MPU6050 callback implementation. Takes the sample data and caclulates the angular position of the cup holder,
   * which is then passed as input to the outer PID controller as the process variable.
   * @param sample Measured accel, gyro, and temp data passed to the callback.
   */
  virtual void hasSample(MPU6050_Driver::MPU6050Sample& sample) override {
    /*
     * The maths here assumes:
     * 1. The MPU is mounted with the chip, SMD components, axis info etc. visible (towards the back) and the text the right way round. README should have a pic.
     * 2. Looking from the back of the cup holder, onto the face of the MPU, a positive angular displacement occurs clockwise, and negative anti-clockwise.
     * 3. Angular displacement is zero when the cup holder is upright.
     */

    // Adjust y accel component for centripetal acceleration caused by angular velocity around axis of rotation
    // Watch units. Sample linear acceleration is in g. Convert to m/s^2.
    // Watch units. Sample angular velocity is in deg/s. Convert to rad/s.
    float ayUnitsCorrected = sample.ay * 9.80665;
    float gzUnitsCorrected = sample.gz * 3.14159265358979323846 / 180.0;
    float ayGrav = ayUnitsCorrected + gzUnitsCorrected * gzUnitsCorrected * radius;

    // Adjust x accel component for tangential acceleration caused by angular acceleration around axis of ratation
    // Watch units. Sample linear acceleration is in g. Convert to m/s^2.
    // Watch units. Sample angular velocity is in deg/s. Convert to rad/s.
    float axUnitsCorrected = sample.ax * 9.80665;
    float axGrav = axUnitsCorrected + ((gzUnitsCorrected - gzPrev) / samplePeriod) * radius;
    gzPrev = gzUnitsCorrected;

    // Caculate magnitude of gravity in xy plane.
    float gravMag = std::sqrt(axGrav * axGrav + ayGrav * ayGrav);

    // Calculate angular displacement in rad from upright.
    float angularPos = std::acos(ayGrav / gravMag);

    // Ensure sign of angular position is correct.
    if (axGrav > 0)
      angularPos = -angularPos;

    // Pass angular position to outer PID controller as PV.
    pidController.calculate(angularPos);
    //std::cout << "MPU working. Data: " << angularPos << std::endl;
    log_file << angularPos << std::endl;
  }

private:
  /**
   * @brief Output file stream for logging MPU measurements.
   */
  std::ofstream log_file{"MPU_log", std::ios::trunc};
  
  /**
   * @brief PID controller object reference attribute.
   */
  PID& pidController;

  /**
   * @brief Radius from axis of rotation to MPU in meters.
   */
  float radius;

  /**
   * @brief Sample period for tangential acceleration calculation in seconds.
   */
  float samplePeriod;

  /**
   * @brief Previous angular velocity around z axis for tangential acceleration calculation (stored in rad/s).
   */
  float gzPrev = 0;
};


int main() {
  // Setup some settings in variables.
  // MPU6050 settings (due to hardware setbacks, these have not been tweaked to achieve optimal performance):
  MPU6050_Driver::Gyro_FS_t MPU_GyroScale = MPU6050_Driver::Gyro_FS_t::FS_250_DPS;
  MPU6050_Driver::Accel_FS_t MPU_AccelScale = MPU6050_Driver::Accel_FS_t::FS_2G;
  MPU6050_Driver::DLPF_t MPU_DLPFconf = MPU6050_Driver::DLPF_t::BW_94Hz;
  uint8_t MPU_SRdiv = 9;
  uint8_t MPU_INTconf = MPU6050_Driver::Regbits_INT_PIN_CFG::BIT_INT_RD_CLEAR;
  uint8_t MPU_INTenable = MPU6050_Driver::Regbits_INT_ENABLE::BIT_DATA_RDY_EN;

  // For an explanation of bellow, see https://invensense.tdk.com/wp-content/uploads/2015/02/MPU-6000-Register-Map1.pdf, page 12.
  float MPU_SamplePeriod;
  if (MPU_DLPFconf == MPU6050_Driver::DLPF_t::BW_260Hz || MPU_DLPFconf == MPU6050_Driver::DLPF_t::RESERVED)
    MPU_SamplePeriod = (1.0 + (float)MPU_SRdiv) / 8000.0;
  else
    MPU_SamplePeriod = (1.0 + (float)MPU_SRdiv) / 1000.0;

  // INA260 settings (due to hardware setbacks, these have not been tweaked to achieve optimal performance):
  INA260_Driver::Alert_Conf INA_AlertMode = INA260_Driver::Alert_Conf::CNVR;
  INA260_Driver::Conv_Time INA_VoltConvTime = INA260_Driver::Conv_Time::TU140;
  INA260_Driver::Conv_Time INA_CurrConvTime = INA260_Driver::Conv_Time::TU4156;
  INA260_Driver::Ave_Mode INA_AveragingMode = INA260_Driver::Ave_Mode::AV1;
  INA260_Driver::Op_Mode INA_OperatingMode = INA260_Driver::Op_Mode::CURCONT;

  // Bellow assumes that only current is being measured (i.e. INA_OperatingMode = CURCONT), which is all we need for this project.
  float INA_SamplePeriod;
  switch (INA_CurrConvTime) {
  case INA260_Driver::Conv_Time::TU140:
    INA_SamplePeriod = 140e-6;
    break;
  case INA260_Driver::Conv_Time::TU204:
    INA_SamplePeriod = 204e-6;
    break;
  case INA260_Driver::Conv_Time::TU332:
    INA_SamplePeriod = 332e-6;
    break;
  case INA260_Driver::Conv_Time::TU588:
    INA_SamplePeriod = 588e-6;
    break;
  case INA260_Driver::Conv_Time::TU1100:
    INA_SamplePeriod = 1100e-6;
    break;
  case INA260_Driver::Conv_Time::TU2116:
    INA_SamplePeriod = 2116e-6;
    break;
  case INA260_Driver::Conv_Time::TU4156:
    INA_SamplePeriod = 4156e-6;
    break;
  case INA260_Driver::Conv_Time::TU8224:
    INA_SamplePeriod = 8224e-6;
    break;
  }

  // Radius from axis of ratation to MPU chip (measured at approx. 15cm):
  float radius = 0.15;

  // I2C device files and addresses for MPU and INA:
  std::string MPU_i2cFile = "/dev/i2c-1";
  std::string INA_i2cFile = "/dev/i2c-0";
  uint8_t MPU_Address = MPU6050_ADDRESS;
  uint8_t INA_Address = INA260_ADDRESS;

  // Gpiod device file path and pins used for interrupts from MPU and INA:
  std::filesystem::path chip_path("/dev/gpiochip4");
  gpiod::line::offset MPU_IntPin = 4;
  gpiod::line::offset INA_IntPin = 5;

  // Motor driver direction GPIO pin:
  gpiod::line::offset MD_DirPin = 23;

  // Set PID constants (due to hardware setbacks, these have not been tweaked to achieve optimal performance)
  double inner_Kp = 0.01;
  double inner_Kd = 0;
  double inner_Ki = 0;
  
  double outer_Kp = 0.01;
  double outer_Kd = 0;
  double outer_Ki = 0;

  //std::cout << "Set up variables." << std::endl;

  // Initialise motor driver object.
  MotorDriver MD20(chip_path, MD_DirPin, 50000);

  //std::cout << "Set up motor driver object." << std::endl;

  // Initialise inner PID controller with callback using motor driver object.
  PID_MotorDriver innerPIDCallback(MD20);
  PID innerPID(&innerPIDCallback, 0, INA_SamplePeriod, std::numeric_limits<double>::max(), std::numeric_limits<double>::lowest(), inner_Kp, inner_Kd, inner_Ki);

  // Initialise outer PID controller with callback using the inner PID controller.
  PID_Position outerPIDCallback(innerPID);
  PID outerPID(&outerPIDCallback, 0, MPU_SamplePeriod, std::numeric_limits<double>::max(), std::numeric_limits<double>::lowest(), outer_Kp, outer_Kd, outer_Ki);

  // Initialise MPU6050 object with callback using the outer PID controller, and I2C callback for communication.
  MPU6050_Feedback MPU6050Callback(outerPID, radius, MPU_SamplePeriod);
  SMBUS_I2C_IF MPU6050_I2C_Callback;
  MPU6050_I2C_Callback.Init_I2C(MPU_Address, MPU_i2cFile);
  MPU6050_Driver::MPU6050 MPU6050(&MPU6050_I2C_Callback, &MPU6050Callback, MPU_IntPin);

  // Initialise INA260 object with callback using the inner PID controller, and I2C callback for communication.
  INA260_Feedback INA260Callback(innerPID);
  SMBUS_I2C_IF INA260_I2C_Callback;
  INA260_I2C_Callback.Init_I2C(INA_Address, INA_i2cFile);
  INA260_Driver::INA260 INA260(&INA260_I2C_Callback, &INA260Callback, INA_IntPin);

  // Setup settings on MPU and INA over i2c.
  MPU6050.InitializeSensor(MPU_GyroScale, MPU_AccelScale, MPU_DLPFconf, MPU_SRdiv, MPU_INTconf, MPU_INTenable, 0, 1); // Given the MPU's orientation, there should be 1g in the Y axis at initalisaton
  INA260.InitializeSensor(INA_AlertMode, INA_VoltConvTime, INA_CurrConvTime, INA_AveragingMode, INA_OperatingMode);

  // Start data aquisition and processing from the MPU and INA.
  MPU6050.begin();
  INA260.begin();

  // Sleep this thread forever.
  while (true)
    std::this_thread::sleep_for(std::chrono::seconds(86400)); // Check once a day.
}

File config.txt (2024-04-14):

# For more options and information see
# http://rptl.io/configtxt
# Some settings may impact device functionality. See link above for details

# Uncomment some or all of these to enable the optional hardware interfaces
dtparam=i2c_arm=on
dtparam=i2c_vc=on,i2c_vc_baudrate=400000
#dtparam=i2s=on
#dtparam=spi=on

# Enable audio (loads snd_bcm2835)
dtparam=audio=on

# Enable PWM on pin 18
# dtoverlay=pwm,pin=18,func=2
dtoverlay=pwm-2chan

# Additional overlays and parameters are documented
# /boot/firmware/overlays/README

# Automatically load overlays for detected cameras
camera_auto_detect=1

# Automatically load overlays for detected DSI displays
display_auto_detect=1

# Automatically load initramfs files, if found
auto_initramfs=1

# Enable DRM VC4 V3D driver
dtoverlay=vc4-kms-v3d
max_framebuffers=2

# Don't have the firmware create an initial video= setting in cmdline.txt.
# Use the kernel's default instead.
disable_fw_kms_setup=1

# Run in 64-bit mode
arm_64bit=1

# Disable compensation for displays with overscan
disable_overscan=1

# Run as fast as firmware / board allows
arm_boost=1

[cm4]
# Enable host mode on the 2711 built-in XHCI USB controller.
# This line should be removed if the legacy DWC2 controller is required
# (e.g. for USB device mode) or if USB support is not required.
otg_mode=1

[all]

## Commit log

2024-02-28 started on cad
    [design.scad]
2024-02-28 Add batu92k's mpu6050 library (https://github.com/batu92k/MPU6050-Sensor-Library-Cpp).
2024-02-28 mostly done cad design
    [design.scad]
2024-02-28 file restructuring
    [design.scad]
2024-02-28 Added files for PID controller
2024-02-29 Implement SMBus I2C interface for MPU6050 library.
2024-03-07 Add I2C block read and write methods to I2C interface class.
2024-03-07 Add SMBus I2C block read and write implementations.
2024-03-11 updated design and 3d print files
    [design.scad, design.stl, housing.stl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]
2024-03-13 lid made
    [design.scad]
2024-03-13 Remove unnecessary double class (PID and PIDImpl) to use just one class (PID).
2024-03-13 corrected mpu bolt radius
    [design.scad]
2024-03-13 Update .gitignore to correctly filter #*# format emacs files.
2024-03-13 Modify PID controller to use callbacks.
2024-03-13 Remove old PID example and README.
2024-03-14 update cad desigh
    [design.scad]
2024-03-18 finalised design for printing
    [design.scad]
2024-03-18 fix accidental paste
    [design.scad]
2024-03-20 added motor driver stuff
2024-03-20 Updated Motor driver code with gpiod library for PWM functioninig_RPI5
2024-03-25 optimise PWM code, change duty cycle output values to nanoseconds and optimise
2024-03-25 shaft elongation on wheel
    [design.scad, wheel.stl]
2024-03-29 Unit test developed for PID calculate function with specified input conditions and call back method based validation
2024-03-29 added cmake for motor driver
2024-03-31 updated wider design and stl export
    [cube.stl, design.scad, frame.stl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]
2024-03-31 added current and voltage read funcions
2024-03-31 power read added
2024-03-31 Modify I2C interface to take the device file used as an argument.
2024-04-01 deleted all unnecessary files to clean Motor Driver folder
2024-04-01 changed cmakelists to include Motor Driver
2024-04-01 Move i2c interface code to its own directory.
2024-04-02 add @brief comments to instances, correct initialisation of MotorDriver in cpp file
2024-04-02 Fix funky bad_alloc et al. caused by nonsense file path by passing file path as argument.
    [main.cpp]
2024-04-02 Deal with opening the PWM period file et al. after writing to export file. Other small changes.
2024-04-02 added modules and optimised slot size
    [design.scad, lid.stl]
2024-04-03 Fix direction control in motor driver code.
2024-04-03 Change header includes to find new i2c_interface.h location.
2024-04-03 Correct GPIO pins for interrupts from MPU6050 and INA260.
2024-04-03 Improve error messages from smbus i2c implementation.
2024-04-03 Unit test case developed for MPU6050 module on various file status monitoring
2024-04-03 Update MPU6050 initialiser to take calibration targets as optional arguments.
2024-04-04 Fix some type errors and add some debug printout.
2024-04-05 Modify INA260 lib to use the big endian I2C word transfers, and fix the logic for setting the Mask/Enable register.
2024-04-05 Record I2C status.
2024-04-05 Record current data for plotting.
2024-04-06 Captured PID source code change and updated declaration
2024-04-06 sample Cmakefile created_yet to work on it
2024-04-07 updating argument error in main program just to get the build running for unit testing
    [main.cpp]
2024-04-08 Fixed I2C communication error
    [main.cpp, mpu6050_AccelOffset_ut.cpp, mpu6050_ut.cpp]
2024-04-09 Implement reading MPU data in one block read for I2C efficiency.
2024-04-09 Modify MPU and INA classes to take interrupt pin number as argument.
2024-04-09 Update MPU and INA testing programs to use new class constructor that takes the interrupt pin number.
2024-04-09 Unit test and cmake file updated for motordriver
2024-04-09 Remove printing to screen when successful.
2024-04-09 Update function call reference issue
    [ina260_ReadCurrent_ut.cpp, ina260_ReadPower_ut.cpp, ina260_ReadVoltage_ut.cpp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]
2024-04-10 Various changes to try debug esoteric errors.
    [ina_testing.cpp, main.cpp, mpu_testing.cpp]
2024-04-10 MPU INA MotorDriver PID unit testing configured to run in a single go!
2024-04-10 Add alternative main program that doesn't use the INA260, in case we cannot resolve our issues with it.
    [main_no_INA.cpp]
2024-04-11 add hardware pin info into README
2024-04-11 changed structure of Hardware text, added description of sensor functionality in README and fixed typos
2024-04-11 Set MPU interrupt input to floating, and INA interrupt input to pull-up.
2024-04-11 add images of gyro position and modify pins+circuitry to readme_materials and implement them into README
2024-04-11 changed svg for circuit again to have white rectangle as background
2024-04-11 added png of circuit with no pull-ups and modified README to not talk about them and use correct image
2024-04-11 Switch I2C busses for new Pi and lower Kp constants for testing.
2024-04-12 Update code to use I2C bus 1 for MPU and change Kp.
2024-04-13 modify circuit with INA after motor, change descriptions in README accordingly and add info about social media
2024-04-13 Wait for interrupt from MPU before reading data from it.
2024-04-13 Current testing parameters.
2024-04-13 Add config.txt file used on our pi for documentation.
    [config.txt]
2024-04-14 Update comments in src/ files. Comment out testing print statements.
2024-04-14 added warning about LC filter and made it optional on the circuitry diagram
2024-04-14 added cad design section to README.md
2024-04-14 Tweak comments in lib/ files. Unlock full range of control for motor driver.
2024-04-14 expand cad section on readme
2024-04-14 Motordriver unit test moved online
2024-04-15 added photos of insta page, changed pins in README and schematic, updated insta statistics
